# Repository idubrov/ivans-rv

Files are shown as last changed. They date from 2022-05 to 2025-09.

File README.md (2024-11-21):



# Ivan's RV-7 Project Log

## Developing

Start a development server:

```bash
npm run install
npm run dev

# or start the server and open the app in a new browser tab
npm run dev -- --open
```

## Building

To create a production version of your app:

```bash
npm run build
```

You can preview the production build with `npm run preview`.

## Published version

Blog is publihed at [https://ivan.aero/](https://ivan.aero/).

## Update the dependencies

Run the following command to update the dependencies:

```bash
npx npm-check-updates --interactive
```

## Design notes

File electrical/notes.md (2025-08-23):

Swiches:

- Flap switch

Rockers

- Master switch (only two busses, but not SDS EFI)
- Beacon // just power
- Landing / Off / Taxi+Flood // 2 pole for light 1+2 / taxi+flood power (same fuse)
- Position / Off / Position + Strobe // 2 pole for strobe / position
- Pitot heat

Colors

- -0 black
- -1 brown
- -2 red
- -3 orange
- -4 yellow
- -5 green
- -6 blue
- -7 violet
- -8 gray
- -9 white
- -90 white/black
- -96 white/blue
- -95 white/green
- -92 white/red
- -94 white/yellow

SENSE bus: 3x22AWG (orange / green / blue)
TRIM bus: 3x22 AWG (gray / white)

Principles:

- Short names for longest running wires

Alerts:

- XPDR fail
- Bus voltage (GEA24)
-

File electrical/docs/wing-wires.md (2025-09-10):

+14AWG red = 19 + 19
+14AWG black = 19 + 19
+18AWG red = 19 + 19
+22AWG red = 17 + 17 + 12 + 24
+22AWG white = 9 + 12 + 7 + 9 + 24
+22AWG black = 9 + 9 + 17 + 17 + 12
+12AWG red = 12
+12AWG black = 12
+20AWG red = 12
+20AWG black = 12
+RG400 = 17 + 17
+3x20AWG shielded = 18 + 18
+2x22AWG shielded = 7 + 12 + 12 + 11 + 12
+3x22AWG shielded = 23 + 10
CANBUS = 17

+M22759/16-22-9 (white): 61 => 100
+M22759/16-22-0 (black): 64 => 100
+M22759/16-22-2 (red): 70 => 100
+M22759/16-20-0 (black): 12 => 20
+M22759/16-20-2 (red): 12 => 20
+M22759/16-18-2 (red): 38 => 50
+M22759/16-14-0 (black): 38 => 50
+M22759/16-14-2 (red): 38 => 50
+M22759/16-12-0 (black): 12 => 20
+M22759/16-12-2 (red): 12 => 20
+M27500-22TE2T14: 54 => 70
+M27500-22TE3T14: 33 => 50
+M27500-20TE3T14: 36 => 50
+M17/128-RG400: 34 => 50

+GF120T-24CANB: 17 => 25

- -0 black
- -1 brown
- -2 red
- -3 orange
- -4 yellow
- -5 green
- -6 blue
- -7 violet
- -8 gray
- -9 white
- -90 white/black
- -96 white/blue
- -95 white/green
- -92 white/red
- -94 white/yellow

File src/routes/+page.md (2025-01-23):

---
title: 'Hello!'
layout: standalone
---

Hello! My name is Ivan, and this is my build log for a Van's Aircraft RV-7 project, #75069.



RV-7 is a side-by-side seat airplane from [Van's Aircraft](https://www.vansaircraft.com/). What you buy from them is a "kit", a set of parts in 4 sub-kits (the empennage, the wings, the fuselage, and the finishing kit). Then it is your job to finish the parts, assemble them into an airframe, and complete it with an engine, avionics plus other pieces to get a functional airplane!

The project is somewhere around the mid-stage. The [fuselage](/category/fuselage) is done to the point where I can start installing various systems. The [empennage kit](/category/empennage) is mostly complete and was mounted to the fuselage.

I started working on both of the wings, and the right-wing is complete to the point where I need to install the top skins.

I have a Superior engine that is close to the Lycoming IO-360-M1B. It is all taken apart and just sits in various boxes.

I am building in my garage at this point. This website is to document the process, both for my entertainment and for documentation purposes.

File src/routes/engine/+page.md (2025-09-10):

---
title: 'Engine'
layout: standalone
---

Engine notes.

Lycoming documents to review:

- SI1014 Lubricating oils
- SI1059 Pre-Lubrication of Parts Prior to Assembly
- SB480 Oil Change Interval
- SI1409 Oil Additive LW16702
- SL180 Preservation for Active and Stored Aircraft
- SB524 Oil Pump Impellers
- SI1505 Cold Weather Starting
- SI171 Spectrometric Oil Analysis
- SI1462 Propeller Oil Control Leak Tests

Sealing pipe threads: https://vansairforce.net/threads/misconceptions-about-pipe-threads.101085/

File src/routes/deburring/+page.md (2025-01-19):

---
title: 'Deburring Tools'
layout: standalone
---

My deburring setup is currently the following:

- 6" Scotch-Brite deburring wheel, 7S Softer (Aircraft Spruce part number [12-00948](https://www.aircraftspruce.com/catalog/topages/scotchdeburrwheel.php)). This is a good universal deburring wheel that leaves very good finish. At the same time, it is relatively aggressive for rounding corners of thin aluminum angles, ribs, skins and so on.
- 6" Scotch-Brite deburring wheel, 7A Medium (Aircraft Spruce part number [12-00875](https://www.aircraftspruce.com/catalog/topages/scotchdeburrwheel.php)). Harder version of the previous wheel. Have not tried to use it yet.
- 1" Scotch-Brite cut and polish unitized wheel (7A Medium), got from [Planetools](https://planetools.com/). Initially used for skin on practice projects, but found that skins cut a groove in the wheel pretty quick.
- 1" aluminum oxide cloth roll (220 grit), from [Amazon](https://www.amazon.com/gp/product/B07D5KVWHD).
- 2" Quick change Scotch-Brite discs (part number 476Z48, Zoro part number [G1197979](https://www.zoro.com/scotch-brite-quick-change-disc-non-woven-8-dia-476z48/i/G1197979). Gray (blue disc) is the softest and works the best for skins.
- Sanding cord, files, sandpaper, Shaviv deburring tools.
- Scotch-brite pads 3M 7447

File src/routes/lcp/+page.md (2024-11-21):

---
title: 'Laser-cut parts status'
layout: standalone
---

This page is a summary of my assessment of the [laser-cut parts issue](https://www.vansaircraft.com/2023/07/information-about-dimpled-hole-cracking-on-some-laser-cut-parts/) that Vans Aircraft announced on July 21st, 2023.

I made a local copy of some of the documents published by Vans Aircraft. Note that these are possibly not the latest versions, just the ones I used at the time.

- [Laser-Cut-Part-List-Revised_R5.6.pdf](/lcp/Laser-Cut-Part-List-Revised_R5.6.pdf)
- [Identification of Laser Cut and Punched Parts](/lcp/Laser-Cut-and-Punched-Part-Identification-Key-with-edits.pdf)
- [Laser-Cut Parts Engineering Evaluation](/lcp/Laser-Cut-Parts-Engineering-Evaluation-R11.3.pdf)

My [inventoring of the laser-cut parts](/blog/2023/08/21/inventoring-laser-cut-parts).

## Status

At the time the fuselage was almost fully assembled, but it only had two potentially "blue" parts ("Acceptable for Use") as per the document -- the F-656 gussets. I remember removing blue plastic from these parts, which made my parts to be the punched ones.

The wing kit has a few parts listed as "red" ("Replacement Recommended"), but all mine are punched ones.

<!-- todo: include a photo of the parts inspected? -->

However, I have pretty much every single part listed in the "blue" category as laser-cut ones, all the wing ribs and the fuel tank baffles. I will be replacing them no matter what. Just one less thing to worry about. Some of them look okay, but the holes are still noticeably out of round.

The empennage kit is a tricky one. I got it shipped somewhere around 4/27/2022, which is after Vans started using third-party vendors to make some of the parts using CNC laser.

Looking at the photos I took when I opened the boxes ([photo 1](1-package-opened.jpeg), [photo 2](2-inventory-parts.jpeg)), it seems like all the long parts have blue plastic film on them, which makes them punched ones. These are the various spars.

Some of the ribs don't have the plastic film. However, I have some experience in hobby machining, and I am confident that I would have noticed if the holes were out of round. So, I think these are punched ones as well. Though, this is not a 100% assessment.

I will look through the photos to see if I can rule out some of the parts as punched ones.

In the grand scheme of things, rebuilding the whole empennage wouldn't be such a hassle if not for the fact that I have already drilled it to the fuselage. However, this is not an unsolvable problem (I'm sure I can figure out a technique to match-drill the holes without damaging the ones in the fuselage).

I don't think I have enough evidence to say I have any laser-cut parts in the empennage, so for now, I will assume it is okay as is (I wouldn't mind rebuilding the rudder, though).

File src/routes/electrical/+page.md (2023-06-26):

---
title: 'Electrical'
layout: standalone
---

Planned electrical equipment / avionics.

## Left wing

- Flyleds Wingtip lighting
  - 3x18AWG shielded cable for POSN-, POSN+, STROBE-, STROBE+
- Flyleds Combo landing light
  - 3x18AWG twisted for the landing light, the taxi light and the ground
- (or) Flyleds landing light
  - 2x14AWG twisted for the landing light and the ground (ground at the wing root)
  - 1x18AWG for the taxi light
- GAP 26 Heated Pitot Tube
  - Pitot input source (to GSU 25)
  - AOA input source (to GSU 25)
  - 2x12AWG twisted for pitot heater
- Van's stall warner
  - 2x22AWG twisted wire
- Archer antenna for NAV in the wingtip
  - RG400 cable
- GTP 59 Temperature probe
  - 3x22AWG shielded cable (to the GSU 25)

## Right wing

- Flyleds Wingtip lighting
  - 3x18AWG shielded cable for POSN-, POSN+, STROBE-, STROBE+
- Flyleds Combo landing light
  - 3x18AWG twisted for the landing light, the taxi light and the ground
- (or) Flyleds landing light
  - 2x14AWG twisted for the landing light and the ground (ground at the wing root)
  - 1x18AWG for the taxi light
- GSA 28 Autopilot roll servo
  - 2x22AWG twisted power / ground
  - 2x22AWG twisted roll trim out
  - 2x22AWG CAN BUS shielded cable (to the panel)
  - 2x22AWG CAN BUS shielded cable (to the GMU 11)
  - 2x22AWG shielded cable for the roll trim motor (to the fuselage)
  - 1x22AWG autopilot disconnect
- GMU 11 Magnetometer in the wingtip
  - 2x22AWG CAN BUS shielded cable (from the roll GSA 28), terminated
  - 2x22AWG twisted power / ground
  - [mount](https://www.steinair.com/product/gmu-11-wing-tip-mount/)
- Camera in the inner access panel (or too annoying for annuals?)
  - RG400 cable for video
  - 2x22AWG twisted power / ground

## Central Fuselage

- Roll trim motor
  - 2x22AWG shielded cable for the roll trim motor (to the GSA 28 roll servo)
  - 3x22AWG shielded cable for the position (to the GEA 24)
- Pilot control stick
  - 1x22 AWG ground
  - 1x22 AWG PTT (to the GMA 245)
  - 2x22 AWG Flaps up/down/gnd (to the GAD 27)
  - 2x22 AWG Pitch trim (to the GAD 27)
  - 2x22 AWG Roll trim (to the GAD 27)
- Co-pilot control stick
  - 1x22 AWG ground
  - 1x22 AWG PTT (to the GMA 245)u
  - 2x22 AWG Flaps up/down/gnd (to the GAD 27)
  - 2x22 AWG Pitch trim (to the GAD 27)
  - 2x22 AWG Roll trim (to the GAD 27)
- Flap Actuator
  - 2x18AWG twisted power (to the GAD 27)
  - 3x22AWG shielded cable for the position (to the GEA 24)

## Aft Fuselage

- GSU 25 ADAHRS unit
  - 2x22AWG CAN BUS shielded cable (to the panel)
  - 2x22AWG CAN BUS shielded cable (to pitch servo)
  - 2x22AWG twisted power / ground
  - 3x22AWG shielded cable (to the GTP 59)
  - pitot tube
  - aoa tube
  - static tube
- GSA 28 Autopilot pitch servo
  - 2x22AWG twisted power / ground
  - 2x22AWG twisted pitch trim out
  - 2x22AWG CAN BUS shielded cable (to the GSU 25), terminated
  - 2x22AWG shielded cable for the pitch trim motor (to the empennage)
  - 1x22AWG autopilot disconnect
- Beacon
  - 2x22AWG twisted power / ground
- ELT Artex 345
  - 3x22AWG shielded cable button and NAV RS

## Empennage

- Flyleds tail light
  - 2x18AWG (or 2X22AWG) shielded cable for TAIL-/TAIL+ (to the empennage)
- Pitch trim motor
  - 2x22AWG shielded cable for the pitch trim motor (to the GSA 28 pitch servo)
  - 3x22AWG shielded cable for the position (to the GEA 24)

## Antennas

- GPS 20A: GA 36 on a glare shield
- GTR 200 (or GTR 20?): DM C63-2 on the belly (in front of the F-705? another behind F-706?)
- (or) GNC 255A: Archer antenna in the wingtip, another DM C63-2 on the belly
- (or) GTN 650: Archer antenna in the wingtip, another DM C63-2 on the belly, GA 36 on a glare shield
- GTX 45R: CI-105, front fuselage
- Artex 345: antenna in front of the stabilizer? Inside the baggage area?

## Chokepoints

### C2: Central Tunnel at F-706

- GSU 25 ADAHRS unit
  - 2x22AWG CAN BUS shielded cable (to the panel)
  - 2x22AWG twisted power / ground
  - 3x22AWG shielded cable (to the GTP 59)
  - Pitot tube
  - AOA tube
- GSA 28 Autopilot pitch servo
  - 2x22AWG twisted power / ground
  - 2x22AWG twisted pitch trim out
  - 1x22AWG autopilot disconnect
- ELT Artex 345
  - 3x22AWG shielded cable button and NAV RS
- Beacon
  - 2x22AWG twisted power / ground
- Flyleds tail light
  - 2X22AWG shielded cable
- Pitch trim motor
  - 3x22AWG shielded cable for the position (to the GEA 24)

Total

- 1x CAN BUS
- 2x tubes
- 9x 22AWG wires
- 3x 3x22AWG shielded cable
- 1x 2X22AWG shielded cable

## Notes

- [Holder for rib lightening holes](https://www.digikey.com/en/products/detail/panduit-corp/LHMS-S6-D/1307127)
- Need to figure out how much real estate is on the turtle deck with Supertracks canopy extension

<!--

TODO: Another / backup GSU-25?

Shielded cable are MIL-C-27500
For Garmin, use MIL-W-22759/16 22AWG or larger, unless otherwise specified. Use MIL-C-27500 for all shielded cable connections.

Temperature probe: next to the inspection panel?
-->

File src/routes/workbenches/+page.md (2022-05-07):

---
title: 'Workbenches'
layout: standalone
---

I made four EAA workbenches total. They are pretty much as per [the original plans](https://www.eaa.org/eaa/aircraft-building/builderresources/while-youre-building/building-articles/tools-and-workshop/worktables), with the following small modifications:

- Framing is 3" shorter and narrower to get 1-1/2" overhang for the table countertop (so I can clamp parts to the table).
- Legs are 3" longer

I used 11 120" (10 feet) 2x4 boards:

| Quantity | Cuts |
| --- | --- |
| 4 | 57" 20-1/2" 20-1/2" 18" |
| 4 | 54" 36" 18" 8-1/2" |
| 2 | 2x36" 18" 18" 8-1/2" |
| 1 | 2x18" 8-1/2" 8-1/2" |
| Total | 4x57" 4x54" 8x36" 8x20-1/2" 14x18" 8x8-1/2" |

I used one full 4'x8' sheet of 3/4" plywood for the tabletop. For the bottom shelves, I used half of the 4'x8' sheet of 1/2" plywood (I could have used two 2'x4' sheets).

One observation here is that EAA workbench plans are not really designed for "manufacturing": shelf plywood uses 24" by 50" (mine got shorter because I made frame narrower). 24" by 48" would work better here, since it would be either a full sheet of 2'x4' plywood or one-quarter of a standard 4'x8' sheet.

You can also [get plans here](http://www.communitygroundworks.org/sites/default/files/workbench_plans_SA1.pdf)

I did not add any casters or any other modifications (yet). Will see how it goes!

The first two tables I primed and painted (I had nothing better to do, I guess). I put "air station" on the first one (filter-regulator-lubricator, plus manifold):



The second table I used for my 8x12 bench lathe and X2 mill. Not that I need them (could be useful for making small fixtures, though), but I gave away their dedicated workbenches when we moved. I just don't want them to rot and rust in the corner. In fact, I even did a [small side project](5-side-project.jpeg) while I was waiting for my RV-7 parts!



The second two tables I only covered with [water-based polyurethane](./4-polyurethane.jpeg). They don't have any specific purpose, I intend to re-arrange them as needed during the build.



I haven't put [DRDT-2](http://experimentalaero.com/products/DRDT-2/DRDT-2.html) dimpler on them nor the backriveting plate. I don't want to permanently modify them just yet, to keep them flexible. For DRDT-2 I am considering "hanging" it between two tables on some sort of a fixture so DRDT-2 throat is at the same height as the tables. Not sure what my plan for backriveting plate is. Might inlay it into the table in the end.

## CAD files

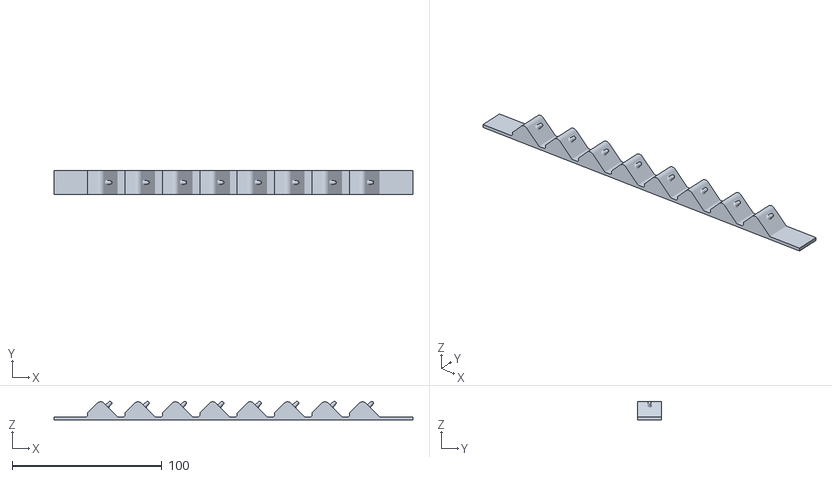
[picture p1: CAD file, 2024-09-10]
static/STLs/PrimeStiffenerHolder.stl
240.0 x 16.0 x 12.4

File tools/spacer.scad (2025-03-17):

$fn = 60;
difference() {
    cylinder(1.8, 10, 10);
    translate([0, 0, -1]) cylinder(6, 5, 5);
}

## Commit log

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2022-05-03 ☀️ Migrating to SvelteKit
2022-05-03 🦋 Implementing basic navigation, categories
2022-05-03 🚜 Migrating content from the old platform
2022-05-03 🐛 Fixing summary mode
2022-05-03 🦩 Redoing categories, removing API, using TypeScript code
2022-05-04 🍯 Updating empennage inventory
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2022-05-04 🏞 Open images and links in the gallery when possible
2022-05-04 🧃 Minor changes, update README.md
2022-05-04 🐜 Some minor tweaks, adding draft mode
2022-05-05 🧶 Fixing thumbnails
2022-05-05 🐿 Vertical stabilizer progress
2022-05-05 🪺 Adding new styles
2022-05-05 🔦 Don't show search box in prod
2022-05-05 🖊 Correcting some typos
2022-05-06 🐁 Default images to 480x360
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2022-05-06 📣 Added telegram channel
2022-05-06 🦇 Removing margins on mobile
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2022-05-06 🦥 Some SCSS reorg
2022-05-06 🌵 Refactoring assets support
2022-05-06 🥔 More image refactoring
2022-05-06 🍕 Fixing incorrect layout hierarchy used for Markdown post / summary
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2022-05-06 🚚 Move icons to /static
2022-05-06 🐎 some style for posts
2022-05-06 🦙 Some style changes
2022-05-06 🐖 temporarily disabling the image
2022-05-06 🪶 Fixing content
2022-05-07 🐆 Fixing links bug, fixing Typescript types
2022-05-07 🦫 markdown fixes
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2022-05-07 🍞 Opening external links in a separate tab
2022-05-07 🎨 Creating paint booth
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2022-05-07 🎃 Fixing incorrect img style
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2022-05-07 🪶 Trying to fix images on Netlify
2022-05-07 🥡 Fixing reactivity issue
2022-05-07 🥊 Fighting more reactivity issues
2022-05-07 🎈 Moving gallery and navlinks to layouts
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2022-05-07 🌅 Some adjustments to images
2022-05-07 🫀 Adjusting images on Netlify
2022-05-07 🪡 Some adjustment to layout in categories, format code
2022-05-07 🩴 Without JS, open images in new tab
2022-05-07 🎩 Don't show gallery when no assets
2022-05-07 🧢 Try to remove menu jumping
2022-05-07 ⛑ Quick fix for grid on mobile
2022-05-08 🐈 Reorganizing how importAssets work
2022-05-08 🐓 Fix for Netlify build
2022-05-09 🐟 Finishing paint booth, updating home page
2022-05-09 🔑 Cofigure lightGallery key
2022-05-09 🍀 Adding RSS feed
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2022-05-10 🎨 Adding update about priming
2022-05-10 💥 Adding images with the damage
2022-05-10 🥾 Disable RSS feed for now
2022-05-10 🦆 Various tiny changes
2022-05-11 🦭 Updating post with the vertical stabilizer riveting
2022-05-11 🕶 Trimmed home page a bit
2022-05-12 🐳 Horizontal stabilizer update
2022-05-13 🌠 Adding image with thick primer
2022-05-13 🐕 Progress on the horizontal spar
2022-05-13 🌅 Push some images
2022-05-14 🎪 Adding another update
2022-05-14 🥁 Re-enable RSS, some renames
2022-05-14 🩼 Trying to fix styles
2022-05-14 🚡 Hiding instagram icon, adding link to README.md
2022-05-14 🛞 Adding draft for the deburring sesion
2022-05-16 🏗 Adding update about deburring
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2022-05-17 ⛱ Moving RSS feed once again
2022-05-17 🏭 Optimize for Feedly
2022-05-18 🦗 Adding another priming session
2022-05-18 💅 Style fixes
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2022-05-19 📸 Added cover photo
2022-05-19 🧤 Adding update: assembling the spars
2022-05-19 👗 Fit image to the screen
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2022-05-21 🐱 Adding new draft
2022-05-21 🐖 First rivets on the skin
2022-05-21 🪲 Fixing a small issue
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2022-05-22 🏞 Adding an image
2022-05-22 🌉 Adding an image
2022-05-24 🐁 Vertical stabilizer front spar
2022-05-24 🐿 Minor update of the last post
2022-05-25 🌴 Vertical stabilizer complete
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2022-05-25 🍕 One more image
2022-05-26 🎮 Adding post about stiffeners
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2022-05-26 🪳 Fixing search issue
2022-06-03 🦉 Priming the stiffeners and the skins
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2022-06-04 🥍 Updating the rudder assembly
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2022-06-06 🎻 Elevator stiffeners
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2022-06-07 🌹 Continuing rudder work
2022-06-08 🥗 Wedge countersiniking, priming
2022-06-09 🥟 Updating the rudder build
2022-06-12 🐹 Adding another update
2022-06-14 🦢 Riveting the rudder
2022-06-14 🦤 Trailing rivets update
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2022-06-16 🪨 Trailing edge update
2022-06-18 🩴 Adding an update
2022-06-19 🎪 Elevator understructure update
2022-06-20 🦑 Priming the skins
2022-06-21 🦘 Riveting stiffeners
2022-06-23 ⚓️ Trimming the counterbalance
2022-06-24 🧚🏻‍♀️ Trim servo support brackets
2022-06-25 🧢 Riveting the stiffeners
2022-06-26 🐰 Drilling the right elevator
2022-06-28 🦞 Priming the right elevator parts
2022-06-29 🐬 Riveting the right elevator
2022-07-05 🧵 The right elevator riveted
2022-07-07 🛷 Preparing the left elevator
2022-07-08 📹 Deburring the left elevator parts
2022-07-09 ⏳ Bending the close-out tabs
2022-07-11 🪫 Priming the parts and new bearing assembly
2022-07-12 🧽 Various small tasks
2022-07-13 📭 Trim tab work
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2022-09-14 🐛 Fixing the page name
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2022-09-23 👻 Fixing assets transformation
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2022-10-02 🥙 Fixing the blog address
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2022-10-07 🪴 Fixing the search
2022-10-07 🪸 Correcting the title
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2022-10-21 🫧 Priming the skin and fitting the new ribs
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2022-10-26 ⚙️ Resetting some rivets
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2022-11-10 🦓 Riveting the seat backs and the pushrods
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2022-12-27 🪃 Fabricating web stiffeners
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2023-01-02 🫒 Riveting center section, fitting the control column
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2023-01-23 🍖 A bit more work on the engine
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2023-02-02 ⛵️ The crotch strap brackets and the aileron trim
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2023-02-19 🪰 Drilled the left step to the skin
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2023-02-26 🎽 Another longeron and stiffener
2023-02-26 🎫 Fitting the stiffeners
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2023-03-04 🐳 Lower longerons and the floor stiffeners
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2023-03-20 🪖 the external step and the floor stiffeners
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2023-04-10 🥦 Riveting the F-704 to the central section
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2023-06-28 🐿️ A bit more work on the fuselage
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2023-07-01 🫎 The aft deck, the rudder brace and the canopy rails
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2023-07-09 🔨 Drilling J-stiffeners
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2023-07-20 🪼 Short priming session
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2023-07-29 🤖 Emulate Netlify image resizing when running dev
2023-07-31 🎒 ClickBond mounts and priming the aft skins
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2023-08-26 🎩 Finished the SB-00036, elevators hinge point, flaps actuator channel
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2023-09-18 🪺 Reworking images metatada: use YAML with width/height/alt
    [3-second-table-machines.meta.yaml]
2023-09-18 🔧 Fixing some of the Svelte warnings
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2023-09-21 🐚 Assembling the FlyLeds landing lights and the controller
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2024-02-23 🐞 Correcting the category
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2024-02-28 📺 Fixing YouTube embed
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2024-03-27 🍴 Tool to generate G-Code to print cleco caps
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2024-04-08 🍩 Working a bit more on the fairings
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2024-07-10 🐛 Fix
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2024-08-31 🐛 Fixing typo
2024-09-03 🎨 More priming and another issue with the ribs
2024-09-03 🦟 Fixing a bug in the YouTube component
2024-09-10 🚎 Deburring the aileron stiffeners
    [PrimeStiffenerHolder.stl]
2024-09-10 🎨 Priming the stiffeners
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2024-09-15 🪡 Working on the aileron stiffeners
2024-09-16 🐦‍🔥 Working on the ribs and the ailerons
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2024-11-21 🐞 Fixes after Svelte 5
2024-11-21 🐜 More fixes
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2024-12-11 🚥 More work on the right fuel tank
2024-12-15 🏜️ Riveting the stiffeners to the skin
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2025-01-28 🐂 A bit more work on the right wing
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2025-03-17 🗓️ Two more entries
    [spacer.scad]
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2025-08-21 🤨 Started working on wiring schematic.
    [electrical.kicad_pcb, electrical.kicad_sch, fuse_aft.kicad_sch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]
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2025-08-23 🎮 Working on electrical schematic
    [electrical.kicad_sch, fuse_aft.kicad_sch, fuse_central.kicad_sch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]
2025-08-23 👊 Try to upgrade versions
    [fuse_aft.kicad_sch]
2025-08-26 📆 Weekend work
    [electrical.kicad_sch, fuse_central.kicad_sch, sensors.kicad_sch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]
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
